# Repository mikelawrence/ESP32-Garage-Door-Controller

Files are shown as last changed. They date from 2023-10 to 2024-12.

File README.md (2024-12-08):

# ESP32 Garage Door Controller
ESPHome based garage door controller. There are a lot of garage door controller projects on the web, what makes this one unique is the use of a rotary encoder to determine garage door position. You need a garage door opener that supports a SPST switch to operate. Some openers (I'm talking about Chamberlain models) don't have this option on the unit. 

On a side note: Chamberlain recently stopped third party API access to MyQ which killed control for all sorts of home automation including Home Assistant. I realize that company's have the right to limit access and to control their ecosystem. But what Chamberlain did was close access to their API after many people bought their opener with third party access available. They also did this so that you will be forced to pay for access your garage door opener from your phone. There is no reason to buy a Chamberlain system when there are other systems that don't charge for access and have open APIs. Vote with your pocketbook and just say NO to Chamberlain Garage Door Openers! 

## Status
* The Entire assembly has been attached to my Genie garage door opener for the last year and has been operating like a champ!

## PCB
PCB is designed in [KiCad](http://kicad.org) which is a great free EDA toolset

## PCB Preview
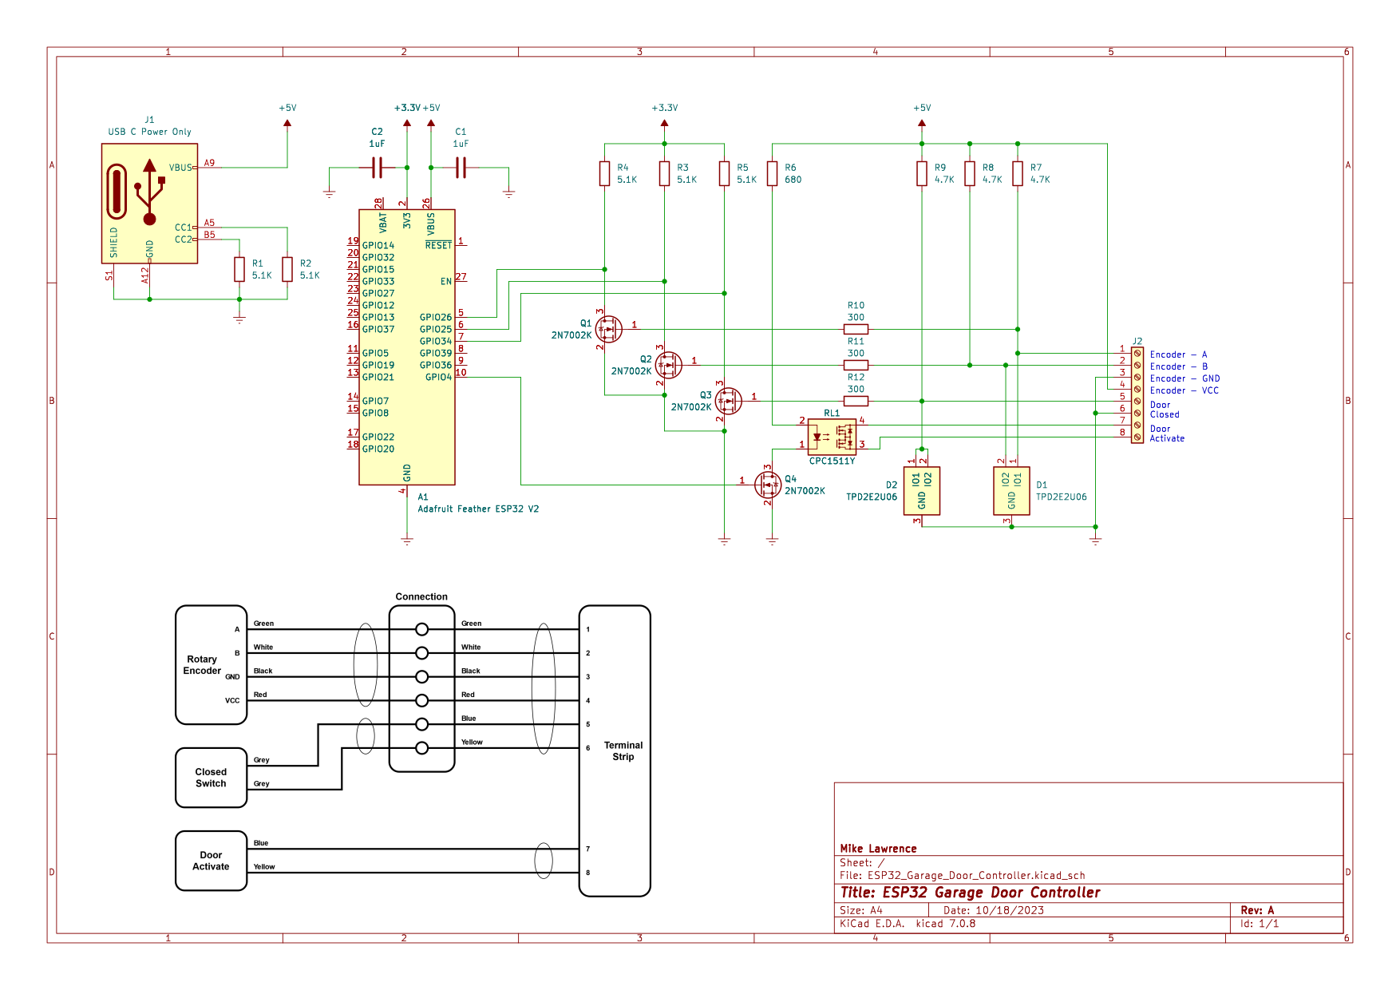
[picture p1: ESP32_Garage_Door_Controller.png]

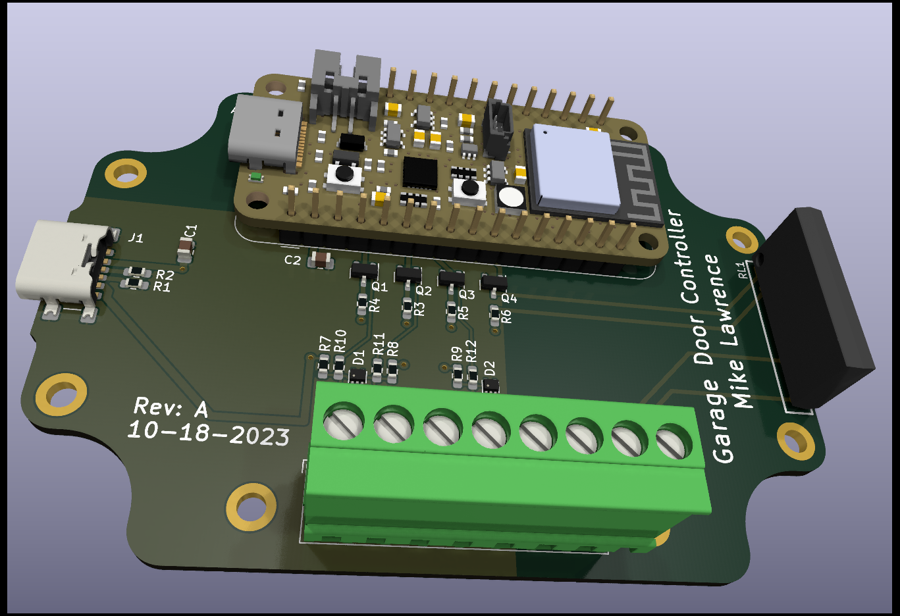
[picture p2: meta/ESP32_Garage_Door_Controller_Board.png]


## PCB Parts List
| Qty | Reference | Value | Description | Manufacturer | Part Number |
| :---  | :--- | :--- | :--- | :--- | :--- |
| 1 | A1 | | Mod, Adafruit Feather ESP32 V2 | Adafruit | 5400 |
| 2 | C1, C2 | 1uF | Cap, Ceramic, 1uF, 10V, 10%, 0805 | Kemet | C0805C105K8RACTU |
| 1 | D1, D2 | | IC, High-Speed ESD Protection Device, SOT-553 | TI | TPD2E2U06DRLR |
| 1 | J1 | | Conn, USB-C Power Only, SMT | GCT | USB4135-GF-A |
| 1 | J2 | | Conn, Terminal Strip, 8-Pos, 3.5 mm | Phoenix Contact | 1843664 |
| 1 | | | Conn, Terminal Strip, 8-Pos, 3.5 mm (mate) | Phoenix Contact | 1863217 |
| 1 | Q1-Q4 | | Trans, N-Ch MOSFET, 60V, 300mA, SOT-23 | OnSemi | 2N7002K |
| 1 | R1-R5 | 5.1k | Res, 5.1k, 100mW, 5%, 0603 | YAGEO | RC0603JR-075K1L |
| 1 | R6 | 680 | Res, 680, 100mW, 5%, 0603 | YAGEO | RC0603JR-07680RL |
| 1 | R7-R9 | 4.7k | Res, 4.7k, 100mW, 5%, 0603 | YAGEO | RC0603JR-074K7L |
| 1 | R10-R12 | 300 | Res, 300, 100mW, 5%, 0603 | YAGEO | RC0603JR-07300RL |
| 1 | RL1 | | IC, Solid State Relay, 230V, 450mA, SIP | IXYS | CPC1511Y |

## 3D Box
I used Autodesk Fusion 360 to design a small clamshell box. This box has holes for 10mm X 3mm round magnets which hold the box pretty securely on a metal opener. There are two version of the box. One has two holes in the lid for standard PG0 gland nuts. The other has three holes for gland nuts.

Use M2.5 brass inserts and M2.5X8mm screws to hold the PCB. Use M3 brass inserts and M3x25mm screws to screw the box halves together. I've included STEP files so that you can 3D Print your own. I've also included the Autodesk Fusion 360 file so you can modify to your heart's content.

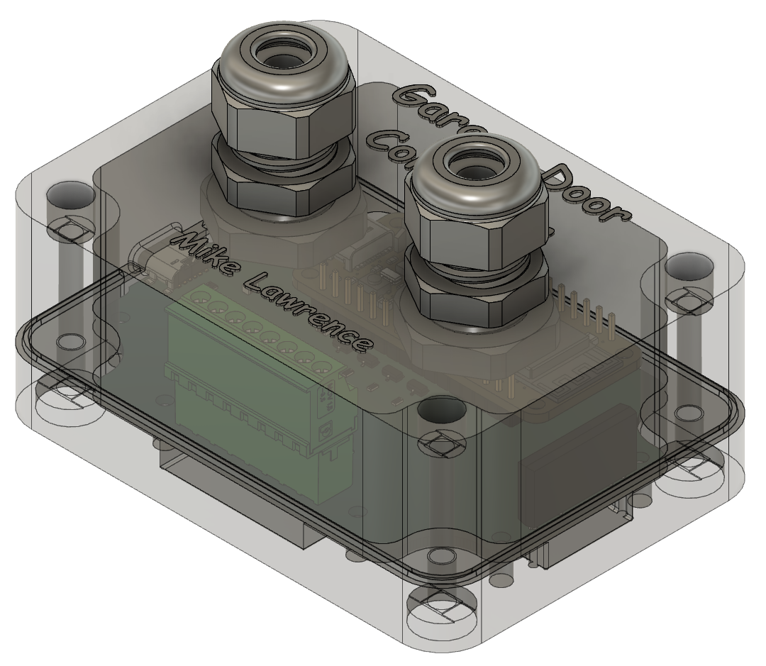
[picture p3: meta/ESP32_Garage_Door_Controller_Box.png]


## Code

```yaml
substitutions:
  name: "car-garage-door"
  friendly_name: "Car Garage Door"
  max_count: "7000"
  invert_encoder: "true"

esphome:
  name: ${name}
  friendly_name: ${friendly_name} 
  name_add_mac_suffix: false

esp32:
  board: adafruit_feather_esp32_v2
  framework:
    type: arduino

# Enable logging
logger:

# Enable Home Assistant API
api:
  encryption:
    key: !secret api_key

# Enable Over-the-Air updates
ota:
  platform: esphome
  password: !secret ota_password

wifi:
  ssid: !secret wifi_ssid
  password: !secret wifi_password
  # using fast_connect since it is required for hidden networks.
  fast_connect: true

  # Captive portal credentials
  ap:
    ssid: "${friendly_name} Hotspot"
    password: !secret hotspot_password

# Enable Fallback WiFi hotspot
captive_portal:

# Enable easy WiFi config via serial port
improv_serial:

globals:
  - id: door_state
    type: int
    restore_value: no
    # CLOSED = 0, OPENING = 1, STOPPED OPENING = 2, CLOSING = 3, STOPPED CLOSING = 4,  OPEN = 5

  - id: max_count
    type: int
    restore_value: no
    initial_value: "${max_count}"

light:
  - platform: neopixelbus
    id: led
    name: "${friendly_name} LED"
    internal: true
    type: GRB
    variant: WS2812
    pin: GPIO0
    num_leds: 1

switch:
  - platform: gpio
    id: button_press
    name: "${friendly_name} Button"
    internal: true
    pin: GPIO4

binary_sensor:
  - platform: gpio
    id: garage_open
    name: "${friendly_name} Sensor"
    pin:
      number: GPIO34
      mode: INPUT
      inverted: true
    device_class: garage_door
    publish_initial_state: true
    filters:
      - delayed_on_off: 50ms
    on_press:
      then:
        - sensor.rotary_encoder.set_value:
            id: position_encoder
            value: 0
        - logger.log: "Closed Switch: Reset Encoder Value"

sensor:
  - platform: rotary_encoder
    id: position_encoder
    name: "${friendly_name} Position"
    internal: true
    pin_a:
      number: GPIO26
      # inverted: true
      mode: INPUT_PULLUP
    pin_b:
      number: GPIO25
      mode: INPUT_PULLUP
    resolution: 1
    min_value: 0
    max_value: 10000
    restore_mode: ALWAYS_ZERO
    publish_initial_value: true
    filters:
    - lambda: !lambda |-
        int min = round(id(max_count) / 50.0);
        int max = id(max_count) - min;
        if (x > max) {
          return 100.0;
        } else if (x < min) {
          return 0.0;
        } else {
          // round to nearest 5 %
          return round(round(x * 100 / id(max_count)) / 5) / 20.0;
        }
    - delta: 0.005

  - platform: wifi_signal
    name: "${friendly_name} WiFi RSSI"
    disabled_by_default: true
    update_interval: 60s
    
  - platform: uptime
    name: "${friendly_name} Uptime"
    disabled_by_default: true
    update_interval: 60s

text_sensor:
  - platform: wifi_info
    ip_address:
      name: "${friendly_name} IP Address"
      disabled_by_default: true

cover:
  - platform: template
    id: template_cover
    name: "${friendly_name}"
    device_class: garage
    optimistic: false
    assumed_state: false
    has_position: true
    lambda: |-
      static double last_position = 0.0;
      static uint32_t last_change = 0;
      double position = id(position_encoder).state;
      auto call = id(led).turn_on();
      call.set_brightness(0.5);
      call.set_transition_length(0);
      if (position == 0.0) {
        id(template_cover).current_operation = CoverOperation::COVER_OPERATION_IDLE;
        id(door_state) = 0;         // CLOSED
        call.set_rgb(0.0,1.0,0.0);  // LED is green
      } else if (position == 1.0) {
        id(template_cover).current_operation = CoverOperation::COVER_OPERATION_IDLE;
        id(door_state) = 5;         // OPEN
        call.set_rgb(1.0,0.0,0.0);  // LED is red
      } else if (last_position < position) {
        id(template_cover).current_operation = CoverOperation::COVER_OPERATION_OPENING;
        id(door_state) = 1;         // OPENING
        call.set_rgb(1.0,0.5,0.0);  // LED is orange
      } else if (last_position > position) {
        id(template_cover).current_operation = CoverOperation::COVER_OPERATION_CLOSING;
        id(door_state) = 3;       // CLOSING
        call.set_rgb(1.0,0.5,0.0);  // LED is orange
      } else if (millis() - last_change > 1000) {
        // the one second wait before recognizing a stopped state allows for bounce when stopped
        id(template_cover).current_operation = CoverOperation::COVER_OPERATION_IDLE;
        if (id(door_state) == 1) {
          id(door_state) = 2;     // STOPPED OPENING
          // if position hasn't changed the cover doesn't publish a current_operation change
          id(template_cover).publish_state();
        } else if (id(door_state) == 3) {
          id(door_state) = 4;     // STOPPED CLOSING
          // if position hasn't changed the cover doesn't publish a current_operation change
          id(template_cover).publish_state();
        }
      }
      if (position != last_position) {
        last_change = millis();
      }
      last_position = position;
      return position;
    open_action:
      - lambda: !lambda |-
          if (id(door_state) == 0) {          // CLOSED
            // CLOSED -> OPENING
            ESP_LOGD("main", "Open action when door is CLOSED, single tap");
            id(single_press).execute();
          } else if (id(door_state) == 1) {  // OPENING
            // already OPENING
            ESP_LOGD("main", "Open action when door is OPENING, do nothing");
          } else if (id(door_state) == 2) {   // STOPPED OPENING
            // STOPPED OPENING(2) -> CLOSING -> STOPPED CLOSING -> OPENING
            ESP_LOGD("main", "Open action when door is STOPPED OPENING, triple tap");
            id(triple_press).execute();
          } else if (id(door_state) == 3) {   // CLOSING
            // CLOSING -> STOPPED CLOSING -> OPENING
            ESP_LOGD("main", "Open action when door is CLOSING, double tap");
            id(double_press).execute();
          } else if (id(door_state) == 4) {  // STOP CLOSING
            // STOPPED CLOSING -> OPENING
            ESP_LOGD("main", "Open action when door is STOPPED CLOSING, single tap");
            id(single_press).execute();
          } else if (id(door_state) == 5) {  // OPEN
            // already OPEN
            ESP_LOGD("main", "Open action when door is OPEN, do nothing");
          }
    close_action:
      - lambda: !lambda |-
          if (id(door_state) == 0) {          // CLOSED
            // already CLOSED
            ESP_LOGD("main", "Close action when door is CLOSED, do nothing");
          } else if (id(door_state) == 1) {   // OPENING
            // OPENING -> STOPPED OPENING -> CLOSING
            ESP_LOGD("main", "Close action when door is OPENING, double tap");
            id(double_press).execute();
          } else if (id(door_state) == 2) {   // STOPPED OPENING
            // STOPPED OPENING -> CLOSING
            ESP_LOGD("main", "Close action when door is STOPPED OPENING, single tap");
            id(single_press).execute();
          } else if (id(door_state) == 3) {   // CLOSING
            // already CLOSING
            ESP_LOGD("main", "Close action when door is CLOSING, do nothing");
          } else if (id(door_state) == 4) {   // STOPPED CLOSING
            // STOPPED CLOSING -> OPENING -> STOPPED OPENING -> CLOSING
            ESP_LOGD("main", "Close action when door is STOPPED CLOSING, triple tap");
            id(triple_press).execute();
          } else if (id(door_state) == 5) {   // OPEN
            // OPEN -> CLOSING
            ESP_LOGD("main", "Close action when door is OPEN, single tap");
            id(single_press).execute();
          }
    stop_action:
      - lambda: !lambda |-
          if (id(door_state) == 0) {          // CLOSED
            // already stopped
            ESP_LOGD("main", "Stop action when door is CLOSED, do nothing");
          } else if (id(door_state) == 1) {   // OPENING
            // OPENING -> STOPPED OPENING
            ESP_LOGD("main", "Stop action when door is OPENING, single tap");
            id(single_press).execute();
          } else if (id(door_state) == 2) {   // STOPPED OPENING
            // already stopped
            ESP_LOGD("main", "Stop action when door is STOPPED OPENING, do nothing");
          } else if (id(door_state) == 3) {   // CLOSING
            // CLOSING -> STOPPED CLOSING
            ESP_LOGD("main", "Stop action when door is CLOSING, single tap");
            id(single_press).execute();
          } else if (id(door_state) == 4) {   // STOPPED CLOSING
            // already stopped
            ESP_LOGD("main", "Stop action when door is STOPPED CLOSING, do nothing");
          } else if (id(door_state) == 5) {   // OPEN
            // already stopped
            ESP_LOGD("main", "Stop action when door is OPEN, do nothing");
          }

script:
  - id: single_press
    then:
    - if:
        # do nothing if another press script is running
        condition:
          and:
            - not:
                script.is_running: double_press
            - not:
                script.is_running: triple_press
        then:
          - switch.turn_on: button_press
          - delay: 0.2s
          - switch.turn_off: button_press
          - delay: 2s

  - id: double_press
    then:
    - if:
        # do nothing if another press script is running
        condition:
          and:
            - not:
                script.is_running: single_press
            - not:
                script.is_running: triple_press
        then:
          - switch.turn_on: button_press
          - delay: 0.2s
          - switch.turn_off: button_press
          - delay: 1s
          - switch.turn_on: button_press
          - delay: 0.2s
          - switch.turn_off: button_press
          - delay: 2s

  - id: triple_press
    then:
    - if:
        # do nothing if another press script is running
        condition:
          and:
            - not:
                script.is_running: single_press
            - not:
                script.is_running: double_press
        then:
          - switch.turn_on: button_press
          - delay: 0.2s
          - switch.turn_off: button_press
          - delay: 1s
          - switch.turn_on: button_press
          - delay: 0.2s
          - switch.turn_off: button_press
          - delay: 1s
          - switch.turn_on: button_press
          - delay: 0.2s
          - switch.turn_off: button_press
          - delay: 2s
```

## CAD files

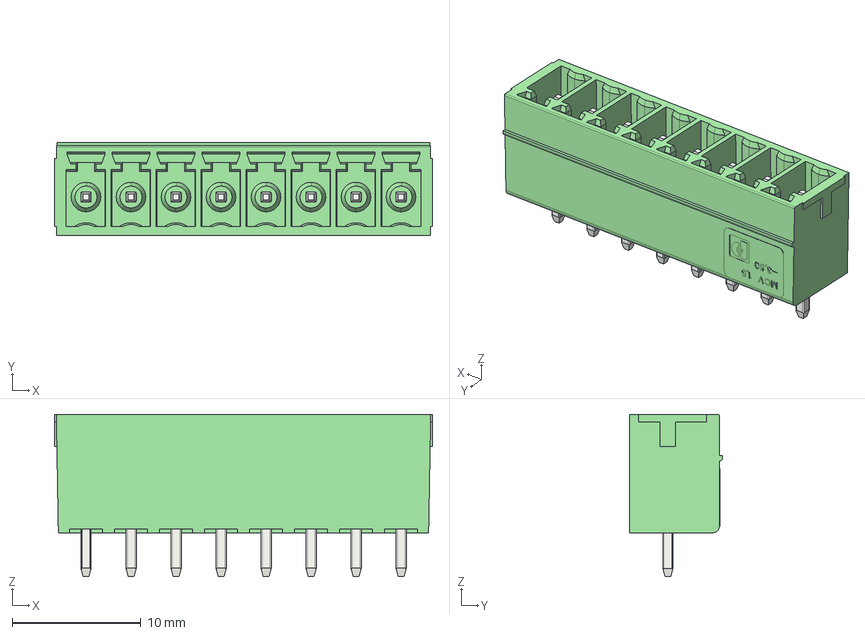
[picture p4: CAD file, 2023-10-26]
3dmodels/pxc_1843664_04_01_MCV-1-5-8-G-3-5_3D.stp
29.4 x 7.25 x 12.6 mm

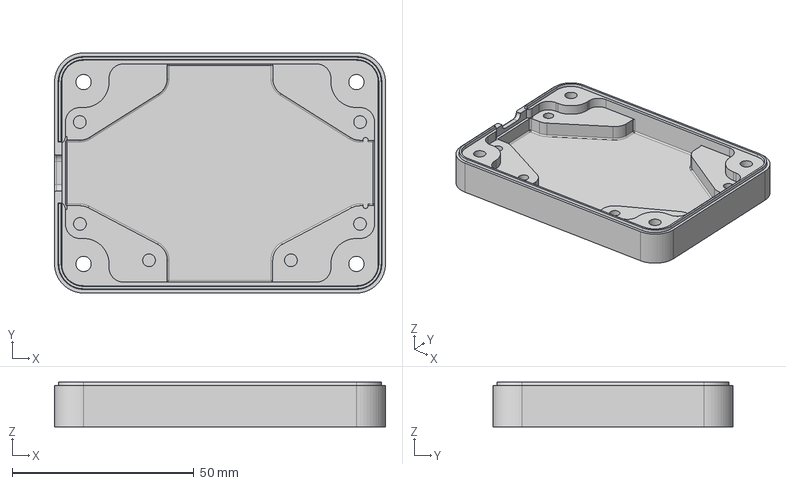
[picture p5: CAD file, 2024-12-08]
box/ESP32 Garage Door Controller Box v41 Bottom Shell.step
91.0 x 66.0 x 12.3 mm

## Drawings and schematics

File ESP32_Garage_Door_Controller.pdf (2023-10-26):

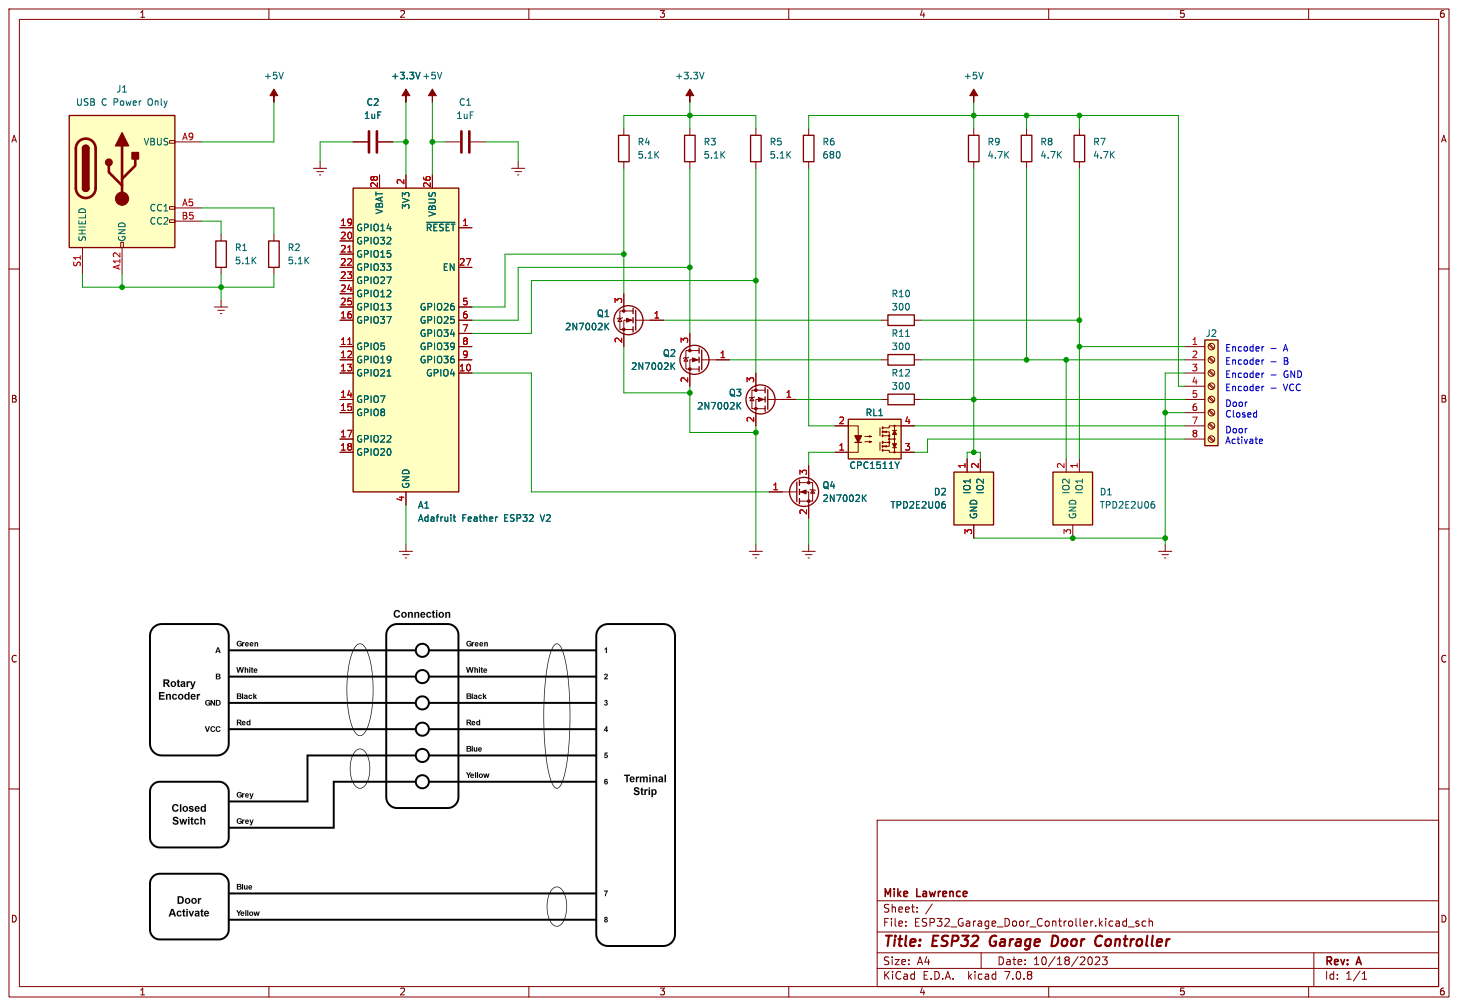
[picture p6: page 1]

2 GPIO32 20 GPIO15 21 GPIO33 22 GPIO27 23 GPIO12 24 GPIO13 25 VBUS 26 EN 27 VBAT 28 GND

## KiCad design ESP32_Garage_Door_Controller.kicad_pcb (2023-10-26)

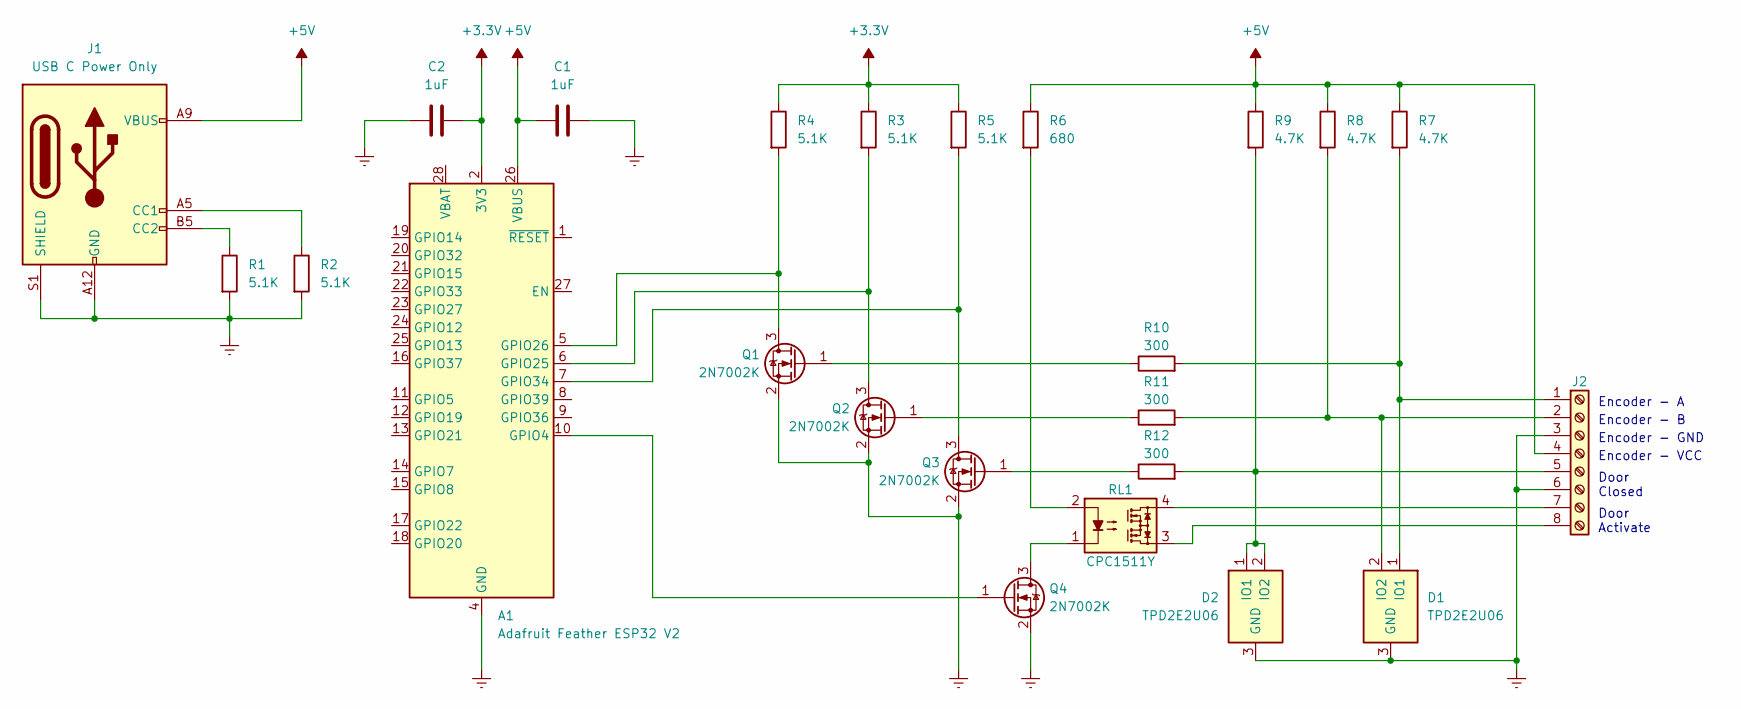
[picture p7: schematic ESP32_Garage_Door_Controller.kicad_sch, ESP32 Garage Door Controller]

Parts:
A1: Adafruit Feather ESP32 V2; Adafruit_ESP32_Feather_V2_5400; Part Number 5400
C1, C2: 1uF; C_0805_2012Metric; Part Number C0805C105K8RACTU
D1, D2: TPD2E2U06; SOT-553; Part Number TPD2E2U06DRLR
J1: USB C Power Only; USB_C_Receptacle_GCT_USB4135-GF-A_6P_TopMnt_Horizontal; Part Number USB4135-GF-A
J2: Screw_Terminal_01x08; PhoenixContact_MCV_1,5_8-G-3.5_1x08_P3.50mm_Vertical; Part Number 1843664
Q1, Q2, Q3, Q4: 2N7002K; SOT-23; Part Number 2N7002K
R1, R2, R3, R4, R5: 5.1K; R_0603_1608Metric_Pad0.98x0.95mm_HandSolder; Part Number RC0603JR-075K1L
R6: 680; R_0603_1608Metric_Pad0.98x0.95mm_HandSolder; Part Number RC0603JR-07680RL
R7, R8, R9: 4.7K; R_0603_1608Metric_Pad0.98x0.95mm_HandSolder; Part Number RC0603JR-074K7L
R10, R11, R12: 300; R_0603_1608Metric_Pad0.98x0.95mm_HandSolder; Part Number RC0603JR-07300RL
RL1: CPC1511Y; Relay_IXYS_PowerSIP; Part Number CPC1511Y

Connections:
+3.3V: A1.2 (3V3), C2.1, R3.1, R4.1, R5.1
+5V: A1.26 (VBUS), C1.2, J1.A9 (VBUS), J1.B9 (VBUS), J2.4, R6.1, R7.1, R8.1, R9.1
GND: A1.4 (GND), C1.1, C2.2, D1.3 (GND), D2.3 (GND), J1.A12 (GND), J1.B12 (GND), J1.S1 (SHIELD), J2.3, J2.6, Q1.2 (S), Q2.2 (S), Q3.2 (S), Q4.2 (S), R1.2, R2.2
unnamed: A1.10 (GPIO4), Q4.1 (G)
unnamed: A1.6 (GPIO25), Q2.3 (D), R3.2
unnamed: A1.5 (GPIO26), Q1.3 (D), R4.2
unnamed: A1.7 (GPIO34), Q3.3 (D), R5.2
unnamed: D1.1 (IO1), J2.1, R7.2, R10.2
unnamed: D1.2 (IO2), J2.2, R8.2, R11.2
unnamed: D2.1 (IO1), D2.2 (IO2), J2.5, R9.2, R12.2
unnamed: J1.A5 (CC1), R2.1
unnamed: J1.B5 (CC2), R1.1
unnamed: J2.7, RL1.4
unnamed: J2.8, RL1.3
unnamed: Q1.1 (G), R10.1
unnamed: Q2.1 (G), R11.1
unnamed: Q3.1 (G), R12.1
unnamed: Q4.3 (D), RL1.1
unnamed: R6.2, RL1.2

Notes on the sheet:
Door Closed
Encoder - B
Encoder - VCC
Encoder - A
Encoder - GND
Door Activate

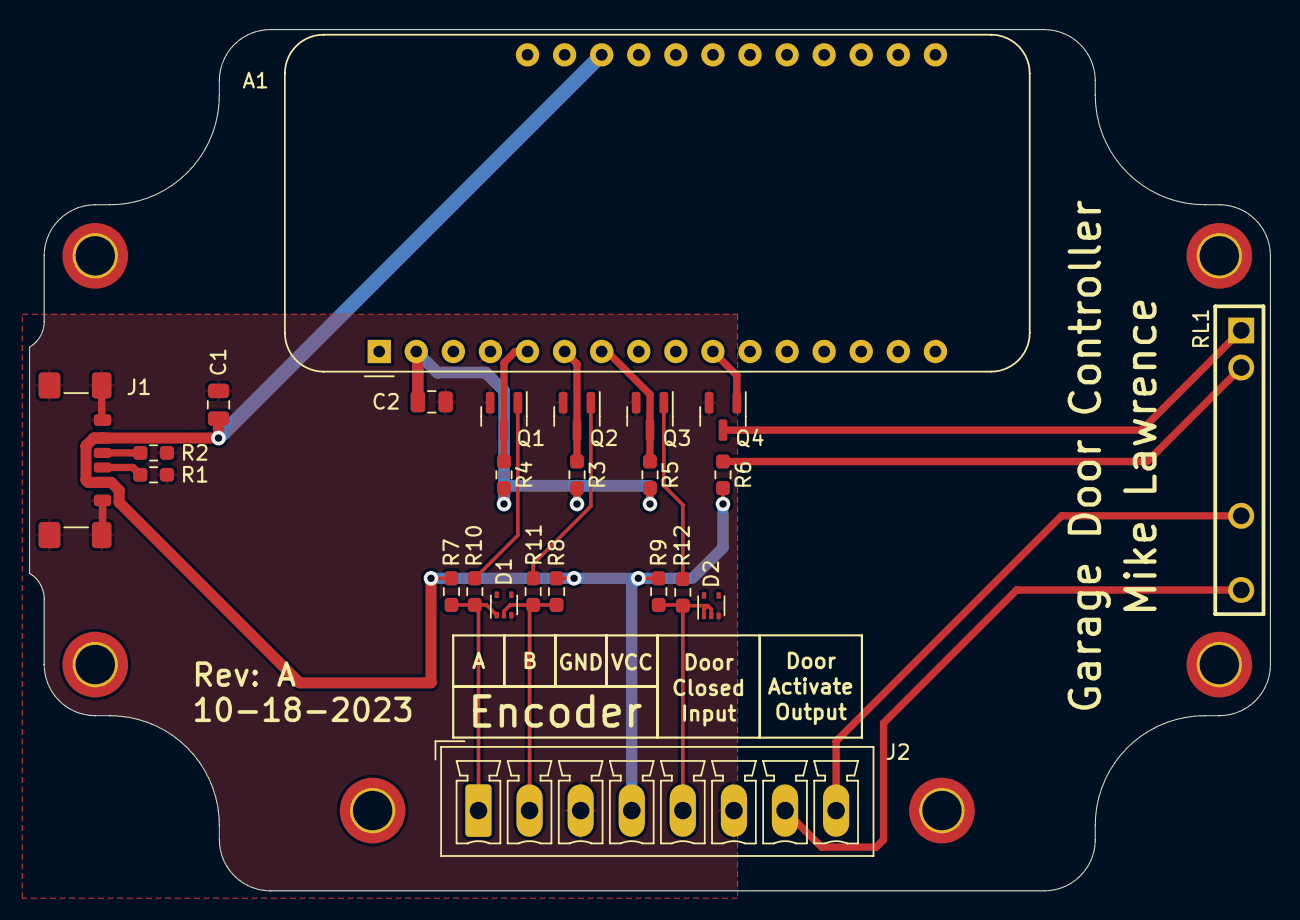
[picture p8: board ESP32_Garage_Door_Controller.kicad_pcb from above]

Board: 2 copper layers, 85.0 x 59.0 mm, 24 parts (0 on the bottom side), 19 nets.

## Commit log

2023-10-26 First commit for project
    [ESP32_Garage_Door_Controller-B_Cu.gbr, ESP32_Garage_Door_Controller-B_Mask.gbr, ESP32_Garage_Door_Controller-Edge_Cuts.gbr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]
2023-10-26 Add .gitignore and add the schematic pdf to the README file
2023-10-26 Add SVG version of the schematic
2023-10-26 Remove SVG schematic and add PNG version of schematic
2023-10-26 Update README to support PNG schematic
2023-10-26 Increase resolution of png schematic
2024-12-08 Add all necessary info to build your own
    Add ESPHome YAML file.
    Add STEP file so you can print your own.Add Autodesk Fusion 360 file.
    [ESP32 Garage Door Controller Box v41 Bottom Shell.step]
2024-12-08 Update Status
    Add note about Chamberlain
